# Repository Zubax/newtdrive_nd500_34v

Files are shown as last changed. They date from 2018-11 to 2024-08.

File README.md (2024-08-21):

# NewtDrive ND500-34V / Zubax Sadulli

Sadulli is an open-hardware reference design of a 500 W integrated propeller drive based on the
[Mitochondrik LV](http://zubax.com/mitochondrik-lv) motor control chip.
It includes a motor and its control electronics in a single compact unit.

The main design goal is to create a compact yet sophisticated motor controller that can be integrated with relatively
small BLDC and PMSM motors (about 40-45 mm in diameter) in a single unit.
Being equipped with a standard mounting hole pattern,
Sadulli can be used as a drop-in replacement for regular standalone motors in various UAV applications.

## Specifications

- Operating voltage range: 4-8S Li-ion LiCoO<sub>2</sub>, 11-34 V
- Maximum continuous power 500 W
- Maximum continuous phase current amplitude 40 A
- [Cyphal](https://telega.zubax.com/)/CAN (formerly UAVCAN) interface compatible with the DS-015 drone standard
- Solderless integration

Sadulli consists of two main parts: a COTS motor and the ESC.
This repository contains the ESC hardware source files only.
There are two design variants of the Sadulli drive.
All of them share the same ESC design.

Variant  | Motor                 | Propeller diameter [inch] | Propeller pitch [inch] | Mass [g]
-------- | --------------------- | ------------------------- | ---------------------- | --------
Alakdan  | Scorpion MII-4010     | 17                        | 6.2                    | 193
Nudo     | N/A                   | N/A                       | N/A                    | 62

Alakdan | Nudo
--|--
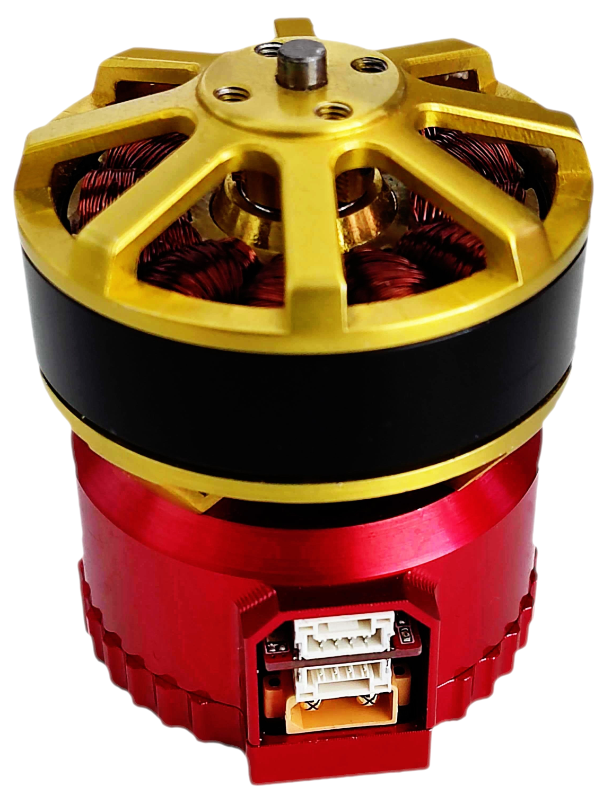
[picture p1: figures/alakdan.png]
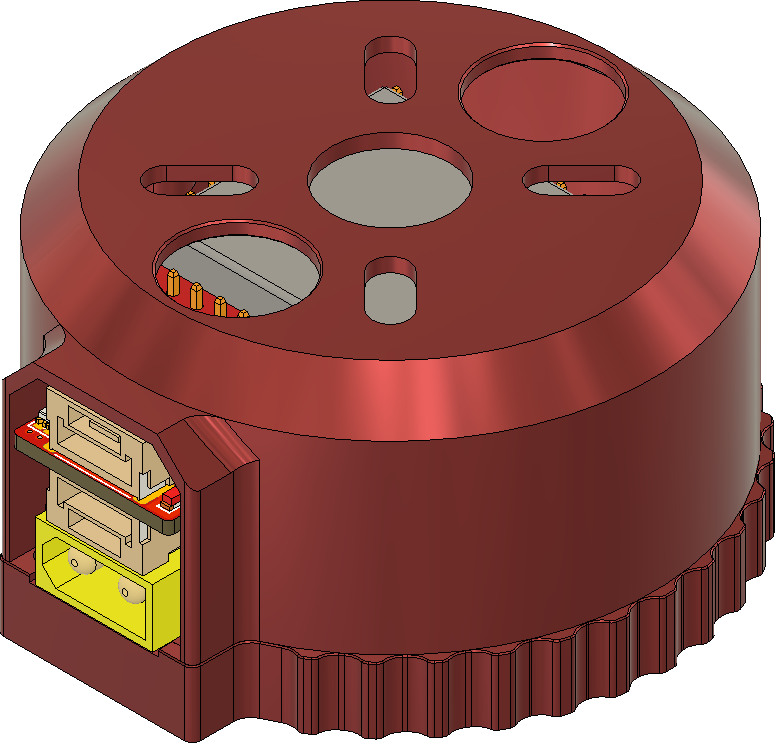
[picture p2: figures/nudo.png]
 | 

Sadulli is equipped with a single non-redundant Cyphal/CAN interface.
The input power is supplied through a standard XT30 male connector.
The device can deliver 5V to the Cyphal/CAN power delivery network if the respective configuration option is enabled.

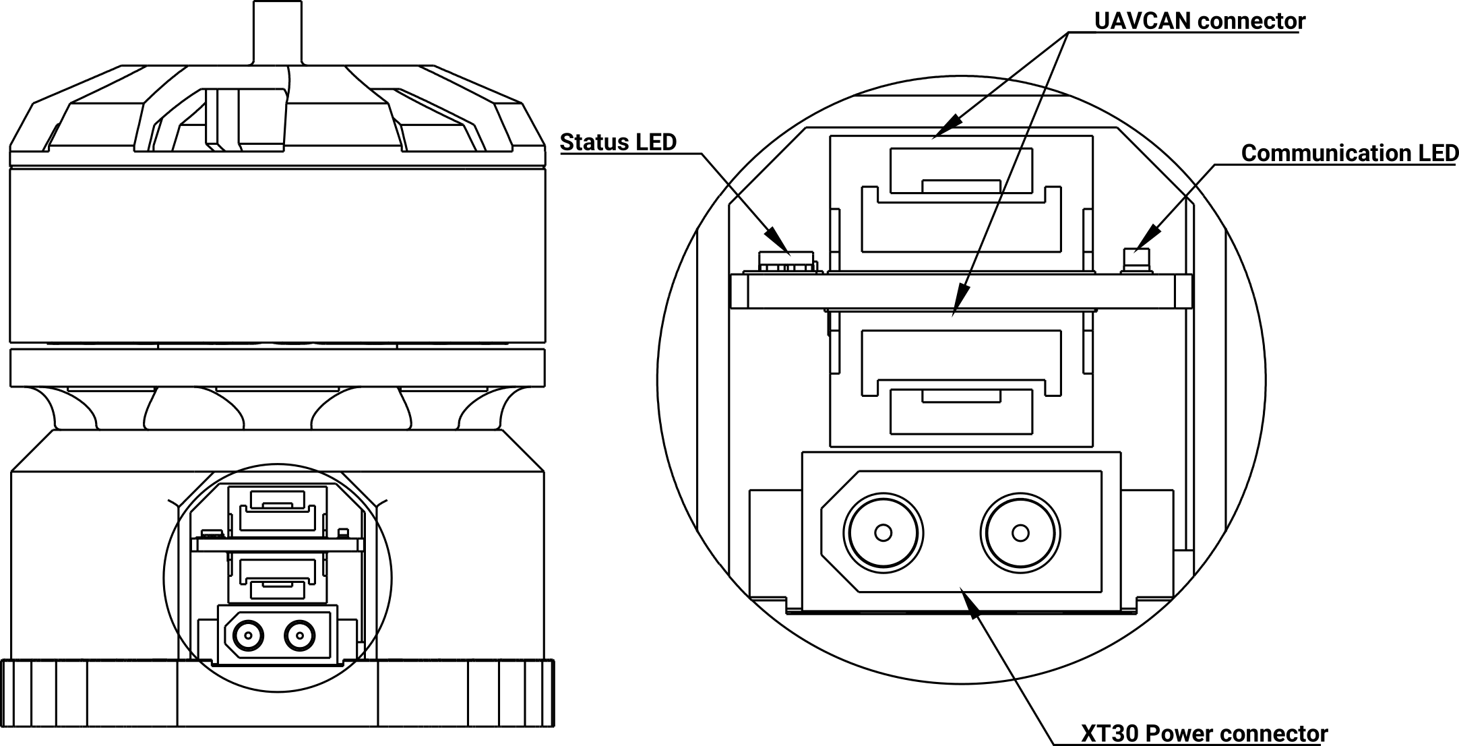
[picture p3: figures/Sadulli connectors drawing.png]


Under the hood, Sadulli is a construction of three PCBs (excluding the Mitochondrik).

<p align="center">
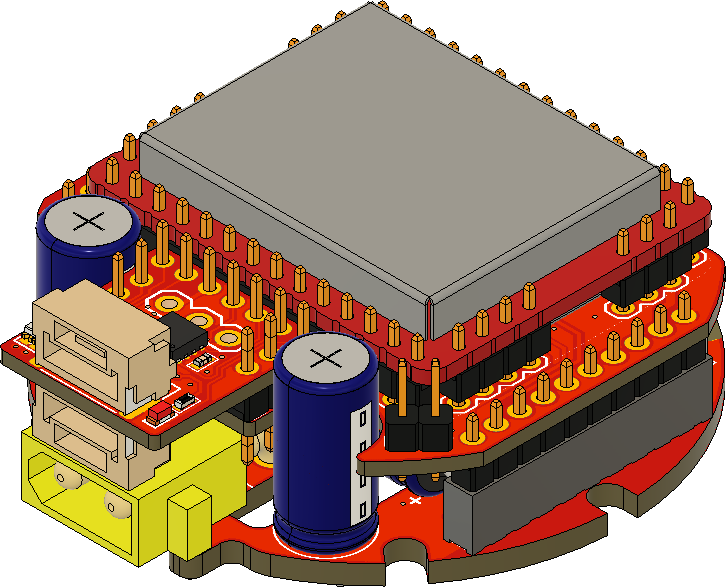
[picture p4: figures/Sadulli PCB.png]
Sadulli PCB

</p>

The main PCB that determines most of Sadulli's properties is the power stage PCB.
The power stage is composed of three [BUK9K6R2-40E](https://www.digikey.com/products/en?keywords=1727-7274-1-ND)
MOSFET arrays.

Parameter                                               | Value
------------------------------------------------------- | -------------------
Drain to Source Voltage (V<sub>ds</sub>)                | 40 V
Current - Continuous Drain (I<sub>d</sub>) @ 25°C       | 40 A
R<sub>ds on</sub> (Max) @ I<sub>d</sub>, V<sub>gs</sub> | 6 mOhm @ 25 A, 10 V
Gate Charge (Q<sub>g</sub>) (Max) @ V<sub>gs</sub>      | 35.4 nC @ 10 V

The resistance of the phase current shunts is 3 mOhm.

The bulk capacitor bank is formed with 6
[68µF aluminum electrolytic capacitors](https://www.digikey.com/product-detail/en/w-rth-elektronik/860020673014/732-8860-3-ND/5727097).

### Telega configuration

The Mitochondrik LV module installed in Sadulli needs to be configured such that it is aware of the parameters of the power stage
(and the motor).
To achieve this, upload the following configuration:

```yaml
# Refer to the Mitochondrik-LV datasheet for the explanation of how the parameter values have been found.
vsi.bridge_resistance:    [0.003, 0.006, 0.003, 0.006, 0.003, 0.003]                            # [ohm]
vsi.phase_current_gain:   [33.333333333333, 33.333333333333, 8.333333333333, 8.333333333333]    # [ampere/volt]
vsi.phase_current_stderr: [0.2, 0.2, 0.1, 0.1]                                                  # [ampere]
vsi.thermistor_v2k:       [223.15, 100.0, 0.0]                                                  # for MCP9700

motor.current_ctl_bwr:  0.04
motor.current_max:      38.0
motor.mechanical_ratio: 7                   # The motor has 14 poles.
motor.inductance_dq:    [29.0e-6, 29.0e-6]
motor.resistance:       0.0508
motor.flux_linkage:     0.002115
motor.current_ramp:     5000.0
motor.voltage_ramp:     20.0
# The thermistor coefficients are valid for:
# R_pull = 1.2 kohms; R_io = 0; V_pull = 3.3 V
# Thermistor models: KTY81/120, KTY81/110, KTY81/121, KTY81/122, KTY81/150, 102PS1J, 102PS1G.
motor.thermistor_v2k: [151.24172662, 36.46076996, 40.65372514]

aux.pull: +1                    # Pull up the thermistor input.

sys.debug: false                # Turn off the in-circuit debug interfaces to enhance EMI immunity.
sys.golden: sys. vsi. motor. aux.pull # Retain these parameter groups across a factory reset.
```

Refer to the Telega Reference Manual for details.

## Release notes

### Sadulli v1.5 (May 2023)

* Added Alakdan variant using Scorpion MII-4010 motor.
* Removed Grosso and Piccino variants using SunnySky motors.
* Updated assembly guide.
* Increased the hardware over-current protection limit (R1 on the connectors PCB increased to 27k).
* Added thermistor alternatives:

Original  | Alternatives
--------- | -----------------
KTY81/120 | KTY81/110, KTY81/121, KTY81/122, KTY81/150, 102PS1J, 102PS1G

### Sadulli v1.0 (January 2021)

First stable release. There have been no substantial changes compared to the pre-production revision.

## License

This project is licensed under the terms of [CC-BY 4.0](https://creativecommons.org/licenses/by/4.0/).

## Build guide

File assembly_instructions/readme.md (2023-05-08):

# Zubax Sadulli V1.5 manufacturing instructions

Prior to starting the assembly make sure that all the items from the list below are present.

Item                          | Amount| Part number                                                            | Description
------------------------------|-------|------------------------------------------------------------------------|-------------------------------------------------------
Motor                         | 1     | Scorpion MII-4010                                                      | BLDC motor for Alakdan.
Housing top                   | 1     |                                                                        | Milled from aluminum.
Housing bottom                | 1     |                                                                        | Milled from aluminum.
Housing screw                 | 4     | DIN 965 20 mm / M2.5x16                                                | Fastening both parts of the housing together.
Motor screw                   | 4     | DIN 7984 4 mm / M3x4                                                   | Fastening the motor to the top part of the housing.
Thermal pad                   | Dia 42 mm | Arctic Cooling ACTPD00018A, ACTPD00005A, or ACTPD00002A            | Sinks the heat to the bottom part of the housing.
Connectors PCB                | 1     |                                                                        |
Logic PCB                     | 1     |                                                                        |
Power stage PCB               | 1     |                                                                        |
Thermistor                    | 1     | NXP KTY81/120, NXP KTY81/110, NXP KTY81/121, NXP KTY81/122, NXP KTY81/150, Littelfuse 102PS1J, or Littelfuse 102PS1G | PTC thermistor with pre-soldered extension wires.

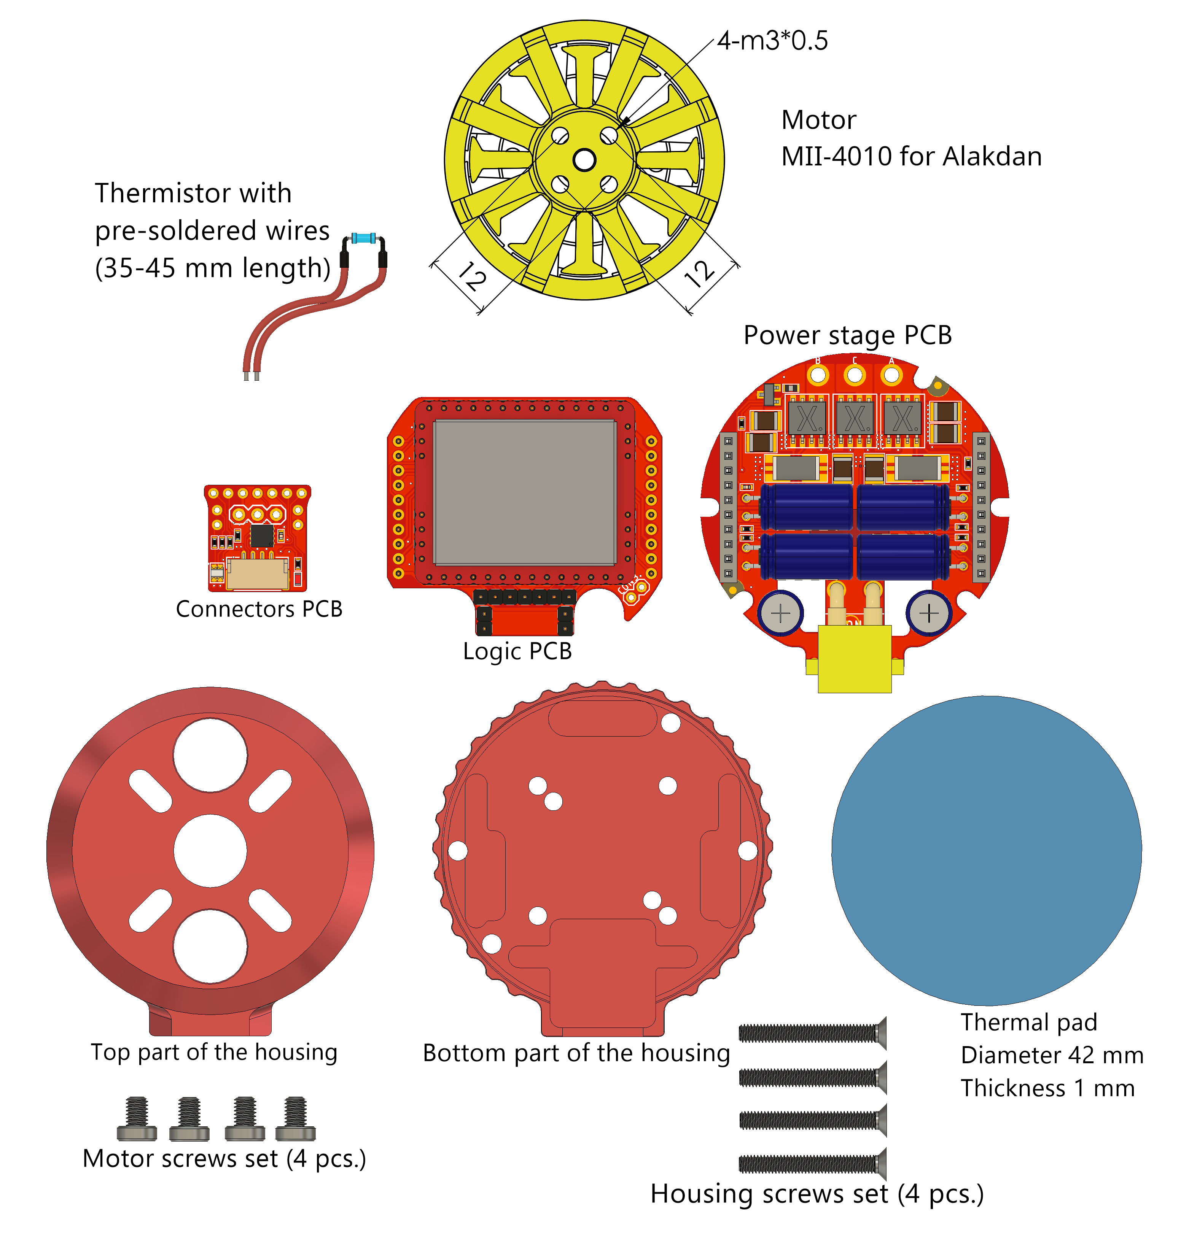
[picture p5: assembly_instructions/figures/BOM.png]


### Assembly Instructions

The whole assembly process may be divided in several sequential steps:

1. Connector and Power stage PCB SMD assembly.

2. Logic PCB assembly. This is manual operation that needs to be precise. 
    * 2 mm male pin headers need to be placed in a repeatable way on the PCB as this may affect assemblability of the device. 
Solder the shorter side to the board ensuring that the headers are straight and at a right andle to the PCB. 
To simplify the process, solder 1 pin first then adjust the angle before soldering the rest. 
    * Attach Mitochondrik LV to the Logic PCB via 2 mm pin headers.
    * Attach Connector PCB to Logic PCB via 2 mm pin headers.
    * Attach the Power stage PCB to Logic PCB via 2 mm pin headers.
    * Refer to the images below for the proper placement.

<p align="center">
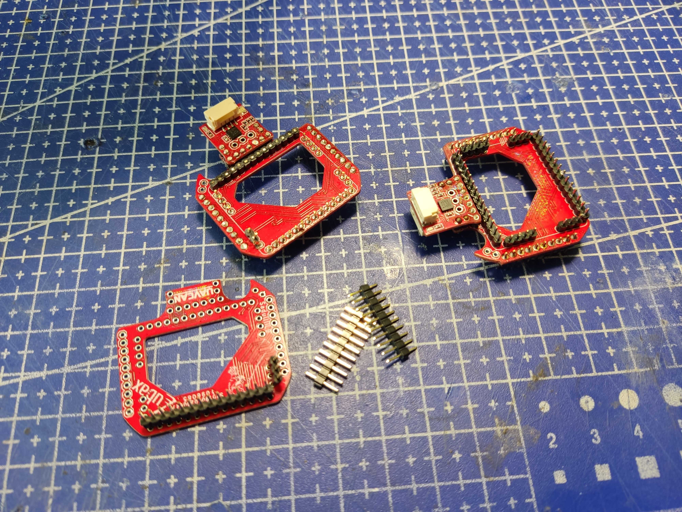
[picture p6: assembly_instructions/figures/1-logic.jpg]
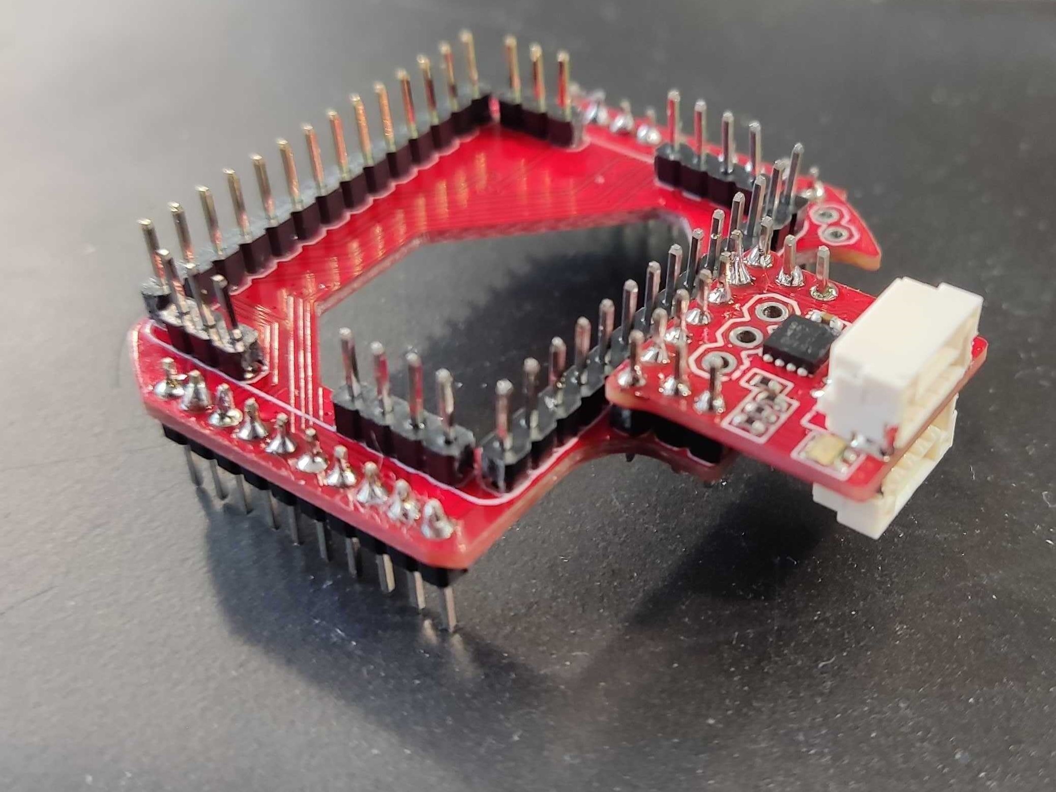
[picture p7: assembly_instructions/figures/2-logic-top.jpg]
<br>
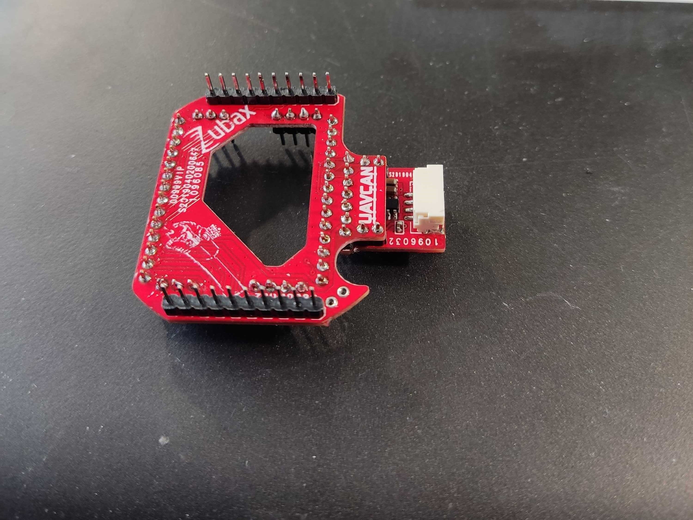
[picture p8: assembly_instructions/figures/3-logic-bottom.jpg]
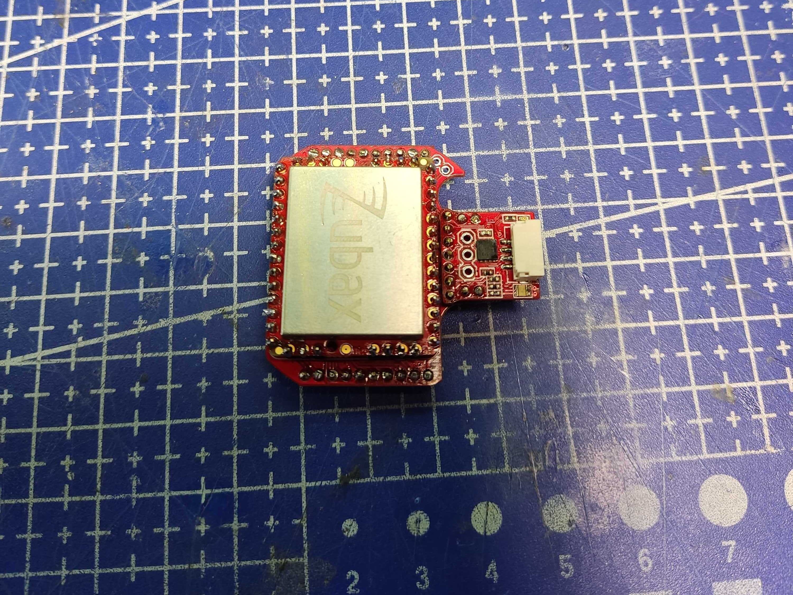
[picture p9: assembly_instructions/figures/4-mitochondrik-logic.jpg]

</p>

3. Motor modification. 
    * Remove the motor retainer ring.
    * The phase wires should be rerouted straight down.

<p align="center">
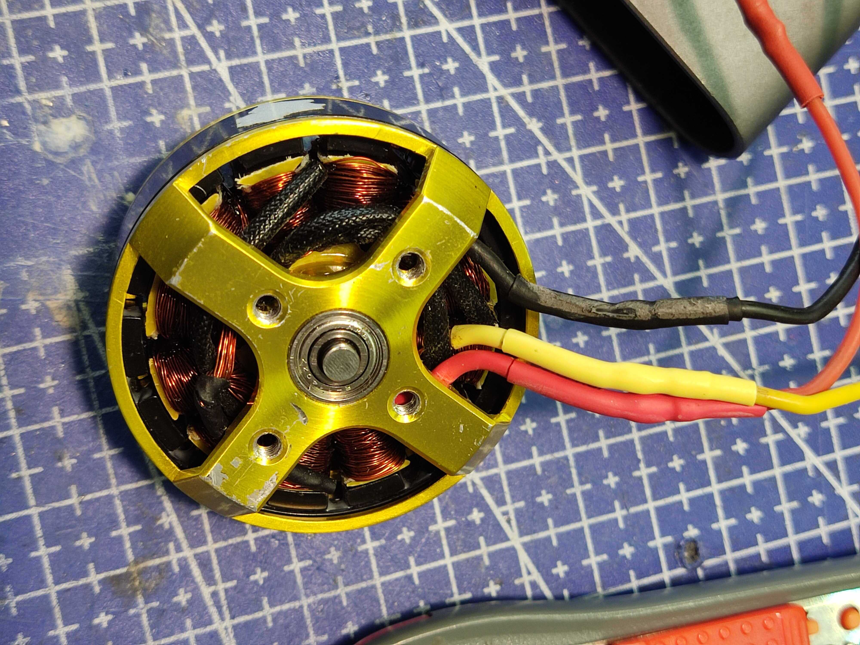
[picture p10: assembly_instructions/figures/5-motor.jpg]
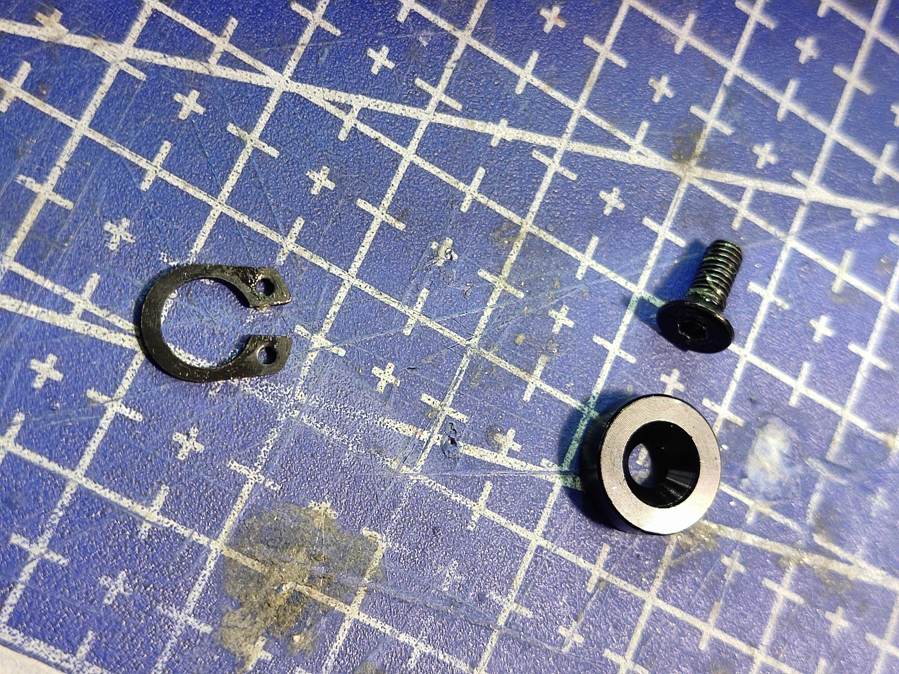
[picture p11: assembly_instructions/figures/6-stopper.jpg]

</p>

4. Thermistor preparation. See photos below for reference.
    * Mix both parts of the epoxy resin in a plastic container using a wooden or plastic mixing tool.
    * Dip the thermistor into the mixture. Only a small amount of glue is needed.
    * The thermistor should be glued directly to the motor windings with epoxy resin
(care must be taken to avoid ingress of epoxy into the motor bearing). Wipe excess with tissue.
    * It can also be placed in between 2 coils, directly on top of a coil, 
or if the coils are flat - glue the side of the thermistor with the flat silver plate.
    * It may be necessary to add more resin to both sides of the thermistor. 
Use a cotton bud to apply more glue carefully.
    * Wait for the epoxy resin to solidify - around 5 minutes.
    * Trim the leads of the thermistor to 2-3 mm.
    * Get 2 pieces of thin wires (0.3-0.6 mm dia). The wires' length should be ~35-45 mm. Remove a portion of the outer casing.
    * Add solder to the ends of the wires (3-5 mm). Add solder to the thermistor leads. 
    * Solder the wire to the lead side-by-side to ensure sufficient contact between the two.
    * Get 2 pieces of the smallest heat shrink tube. Cut to 2-3 mm in length. Cover the connection point and apply heat with a heat gun.

<p align="center">
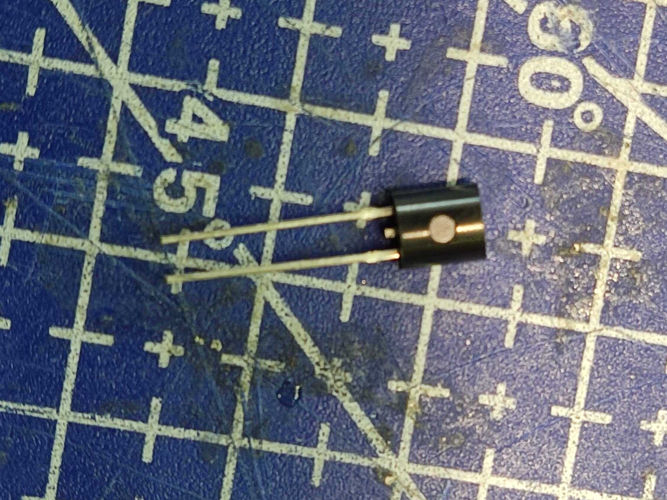
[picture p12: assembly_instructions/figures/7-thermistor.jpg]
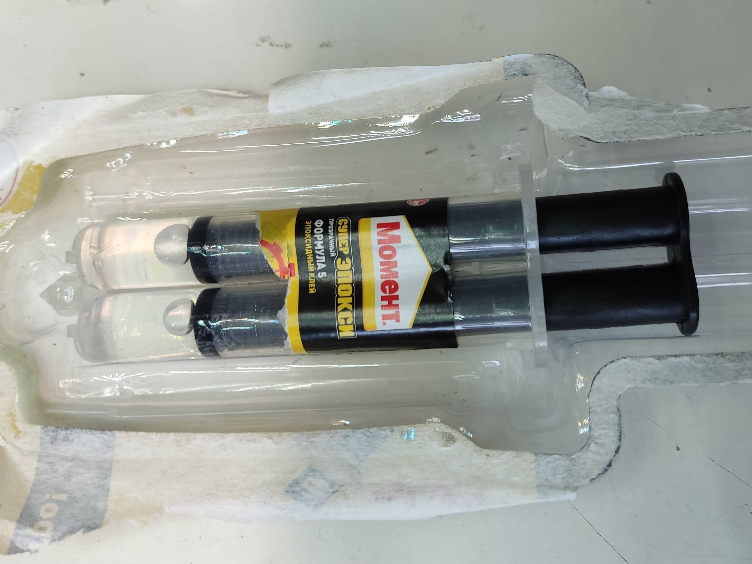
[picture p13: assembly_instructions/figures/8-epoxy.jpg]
<br>
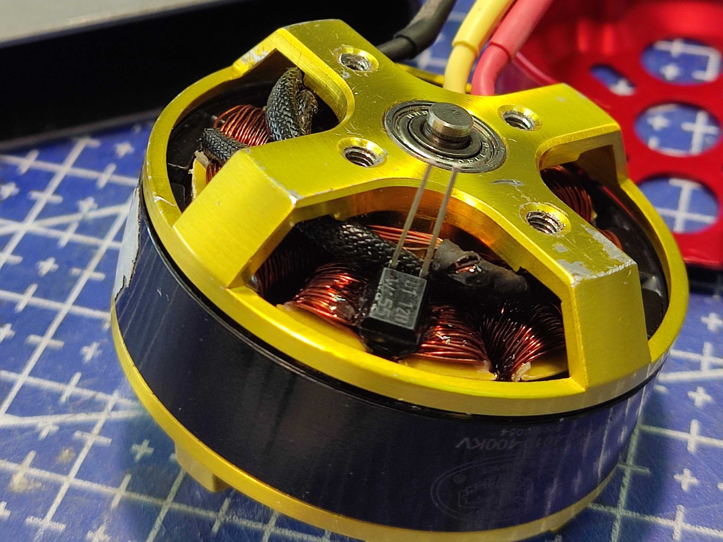
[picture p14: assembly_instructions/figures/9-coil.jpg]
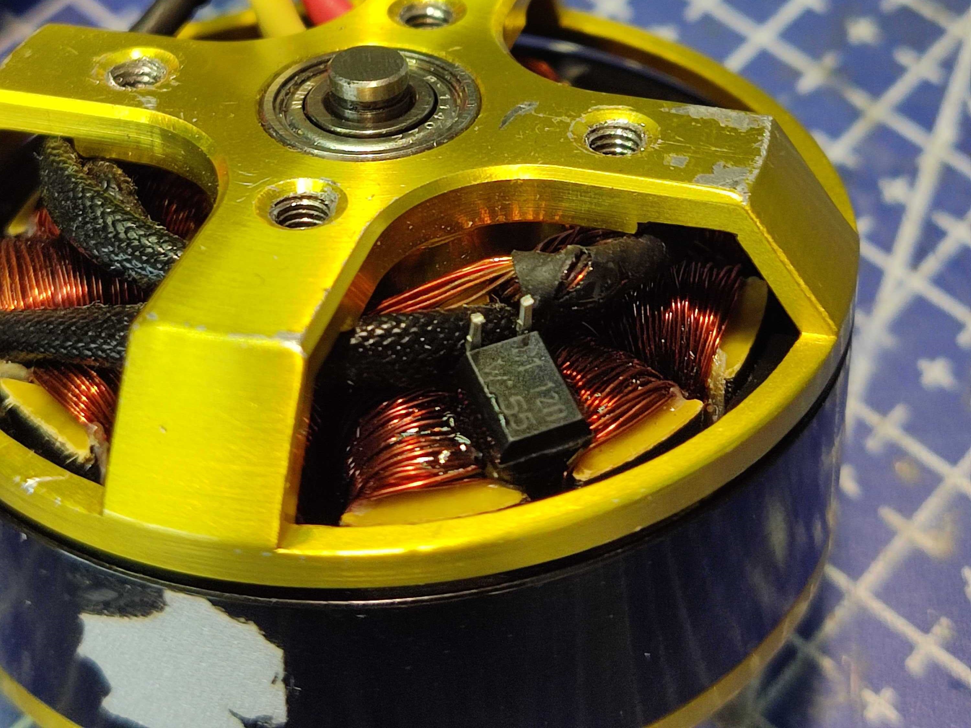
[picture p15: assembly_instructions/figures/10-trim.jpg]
<br>
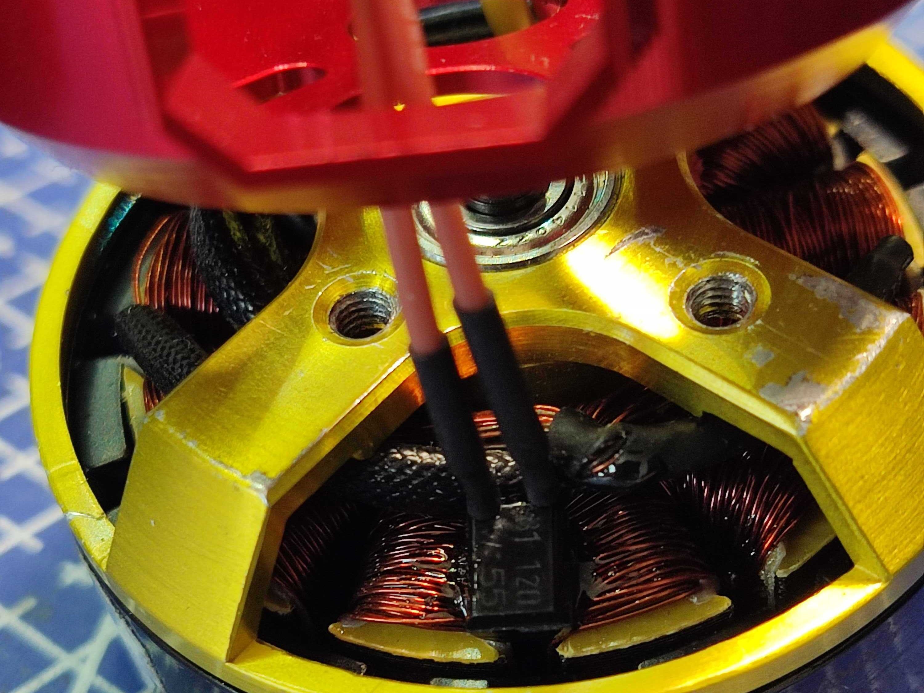
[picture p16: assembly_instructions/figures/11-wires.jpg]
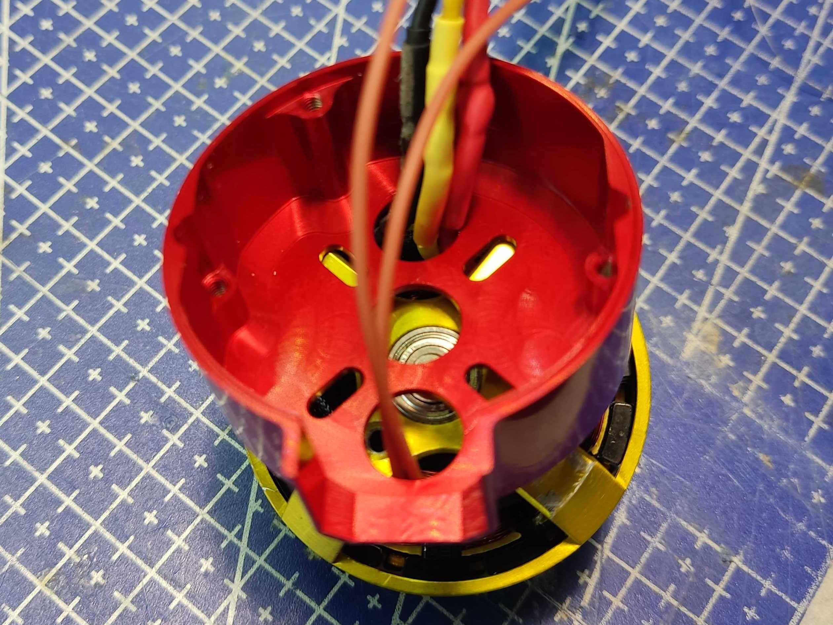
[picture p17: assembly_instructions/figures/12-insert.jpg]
<br>
</p>

5. Housing Attachment. See photos for reference.
    * Insert the motor phase wires and the thermistor wires through the housing holes. Ensure proper placement.
    * Get 4 pieces of DIN 7984 4 mm (motor screws). Attach the motor to the top housing. Use threadlock glue.
Ensure that the screws don't touch the coils and that no moving part of the motor is touching the enclosure.
    * Trim the motor phase wires to ~30-35 mm (measuring from the bottom of the motor).
    * Remove the insulation. Twist the wires. Add solder to the ends of each wire (3-5 mm).
    * Place the assembly on a vise to secure it. Use rubber protection pads so that the motor isn't scratched.
    * Solder the phase wires to 3 pads on the PCB.
    * **The phase wires shall be soldered such that a positive setpoint drives the motor clockwise (viewed from the top).**
If the observed direction is different, any two phase wires of the three are to be swapped.
    * Trim the thermistor wires and solder to 2 pads on the PCB. See photo for correct placement.
    * Add thermal pad to the inside of the bottom housing. 
    * The thermal pad has the shape of a circle with a diameter of 40-42 mm, 1 mm thickness.
    * Attach bottom housing to the top housing using 4 housing screws (DIN 965 20 mm / M2.5x16)

<p align="center">
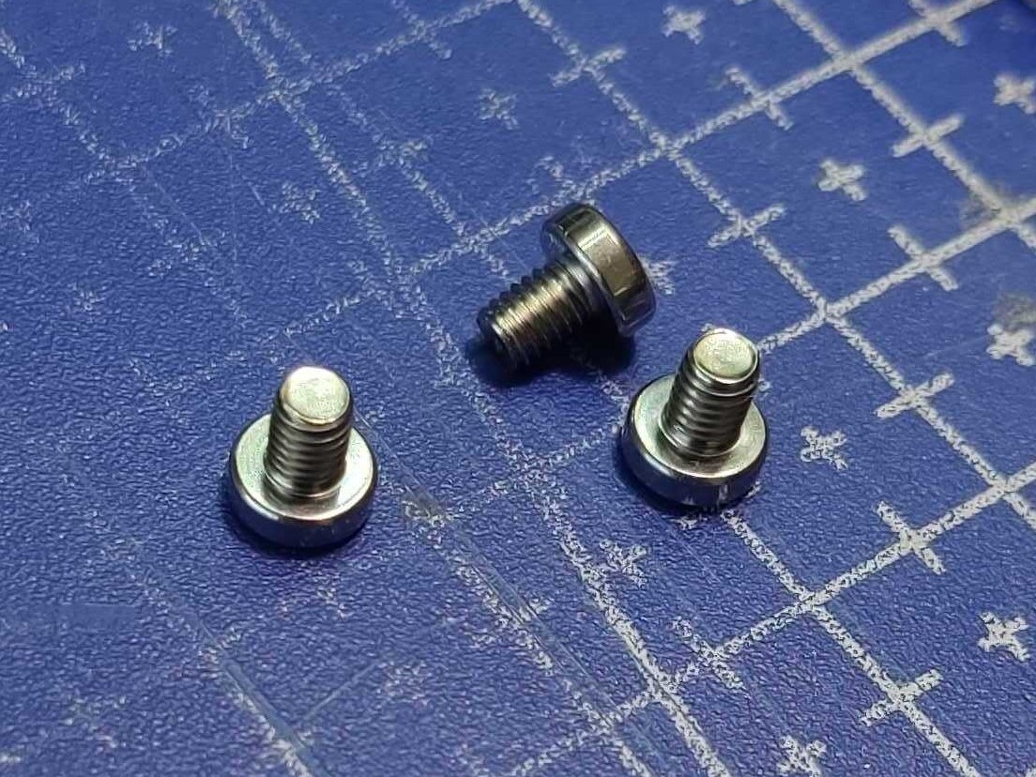
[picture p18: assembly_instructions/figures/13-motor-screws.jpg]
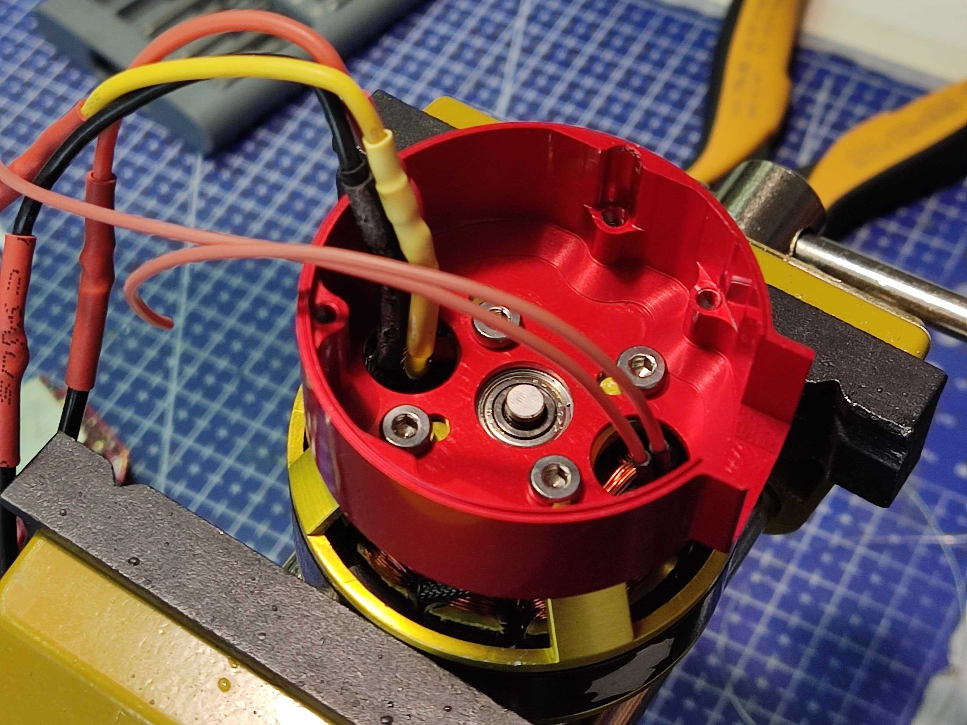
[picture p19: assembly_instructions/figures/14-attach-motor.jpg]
<br>
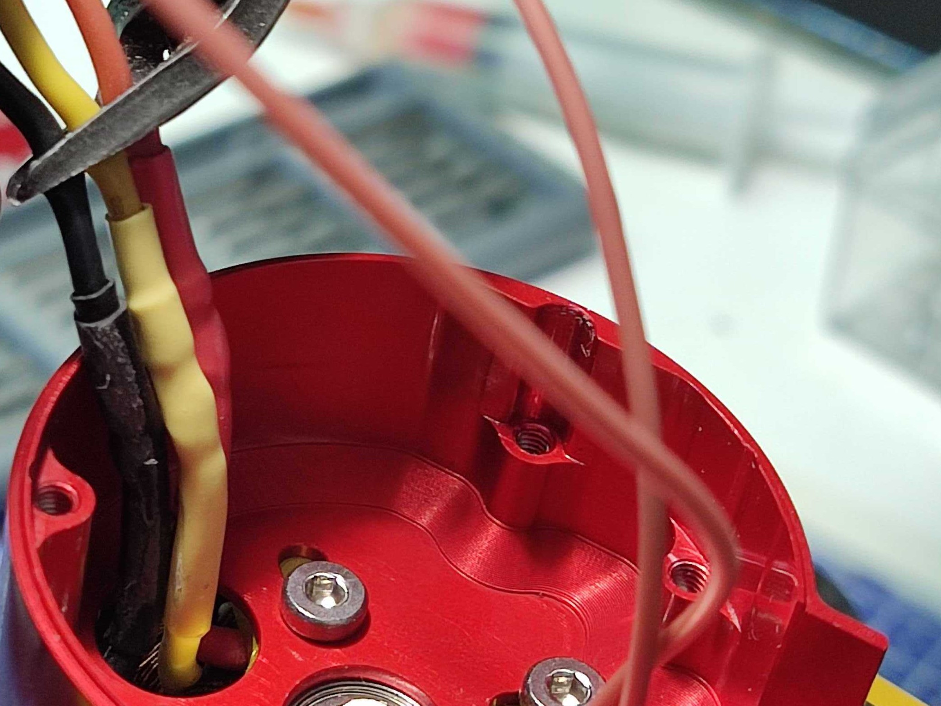
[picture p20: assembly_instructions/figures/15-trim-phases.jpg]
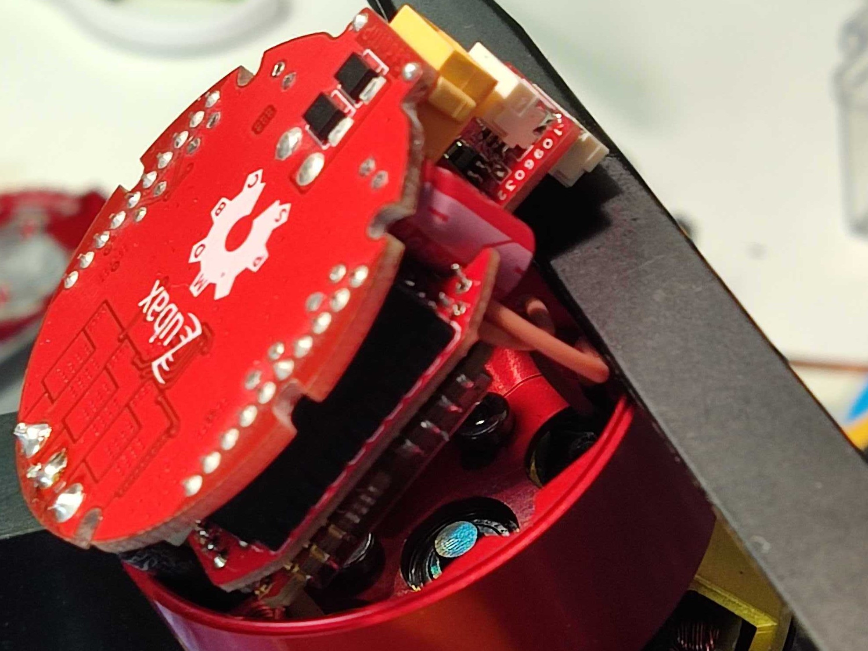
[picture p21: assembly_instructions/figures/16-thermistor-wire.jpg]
<br>
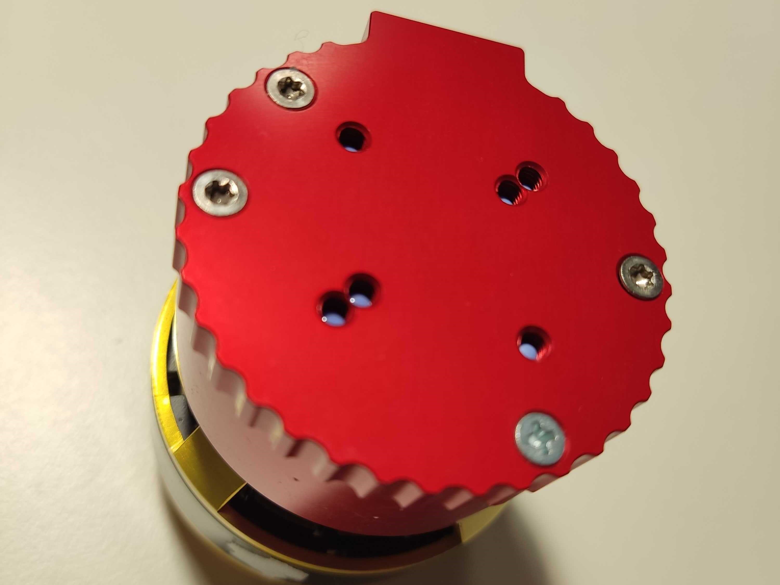
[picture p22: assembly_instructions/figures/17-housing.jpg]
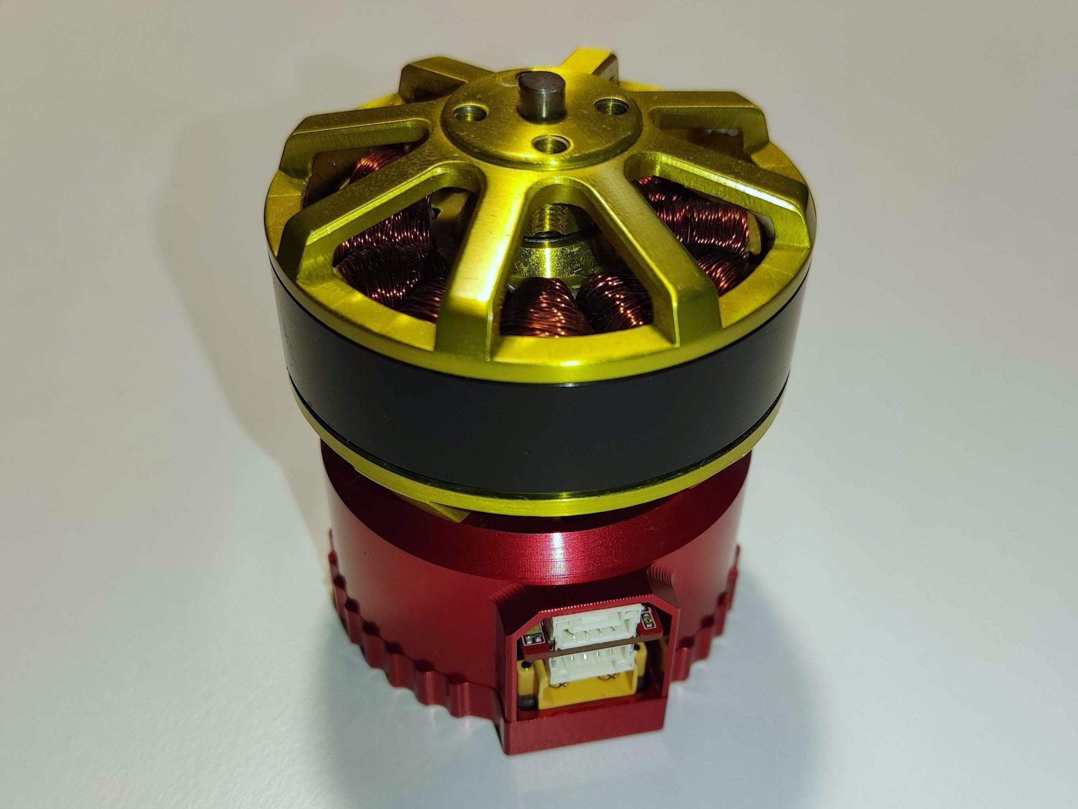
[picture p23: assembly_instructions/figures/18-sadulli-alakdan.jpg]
<br>
</p>

6. Test using DrWatson (internal).
    * **If the motor spins counterclockwise (viewed from the top) during the DrWatson test, remove the bottom housing and swap any two phase wires.**

For the detailed assembly process of Sadulli v1.0 (Grosso/Piccino) please check the video: https://youtu.be/bqTBei1wUUw

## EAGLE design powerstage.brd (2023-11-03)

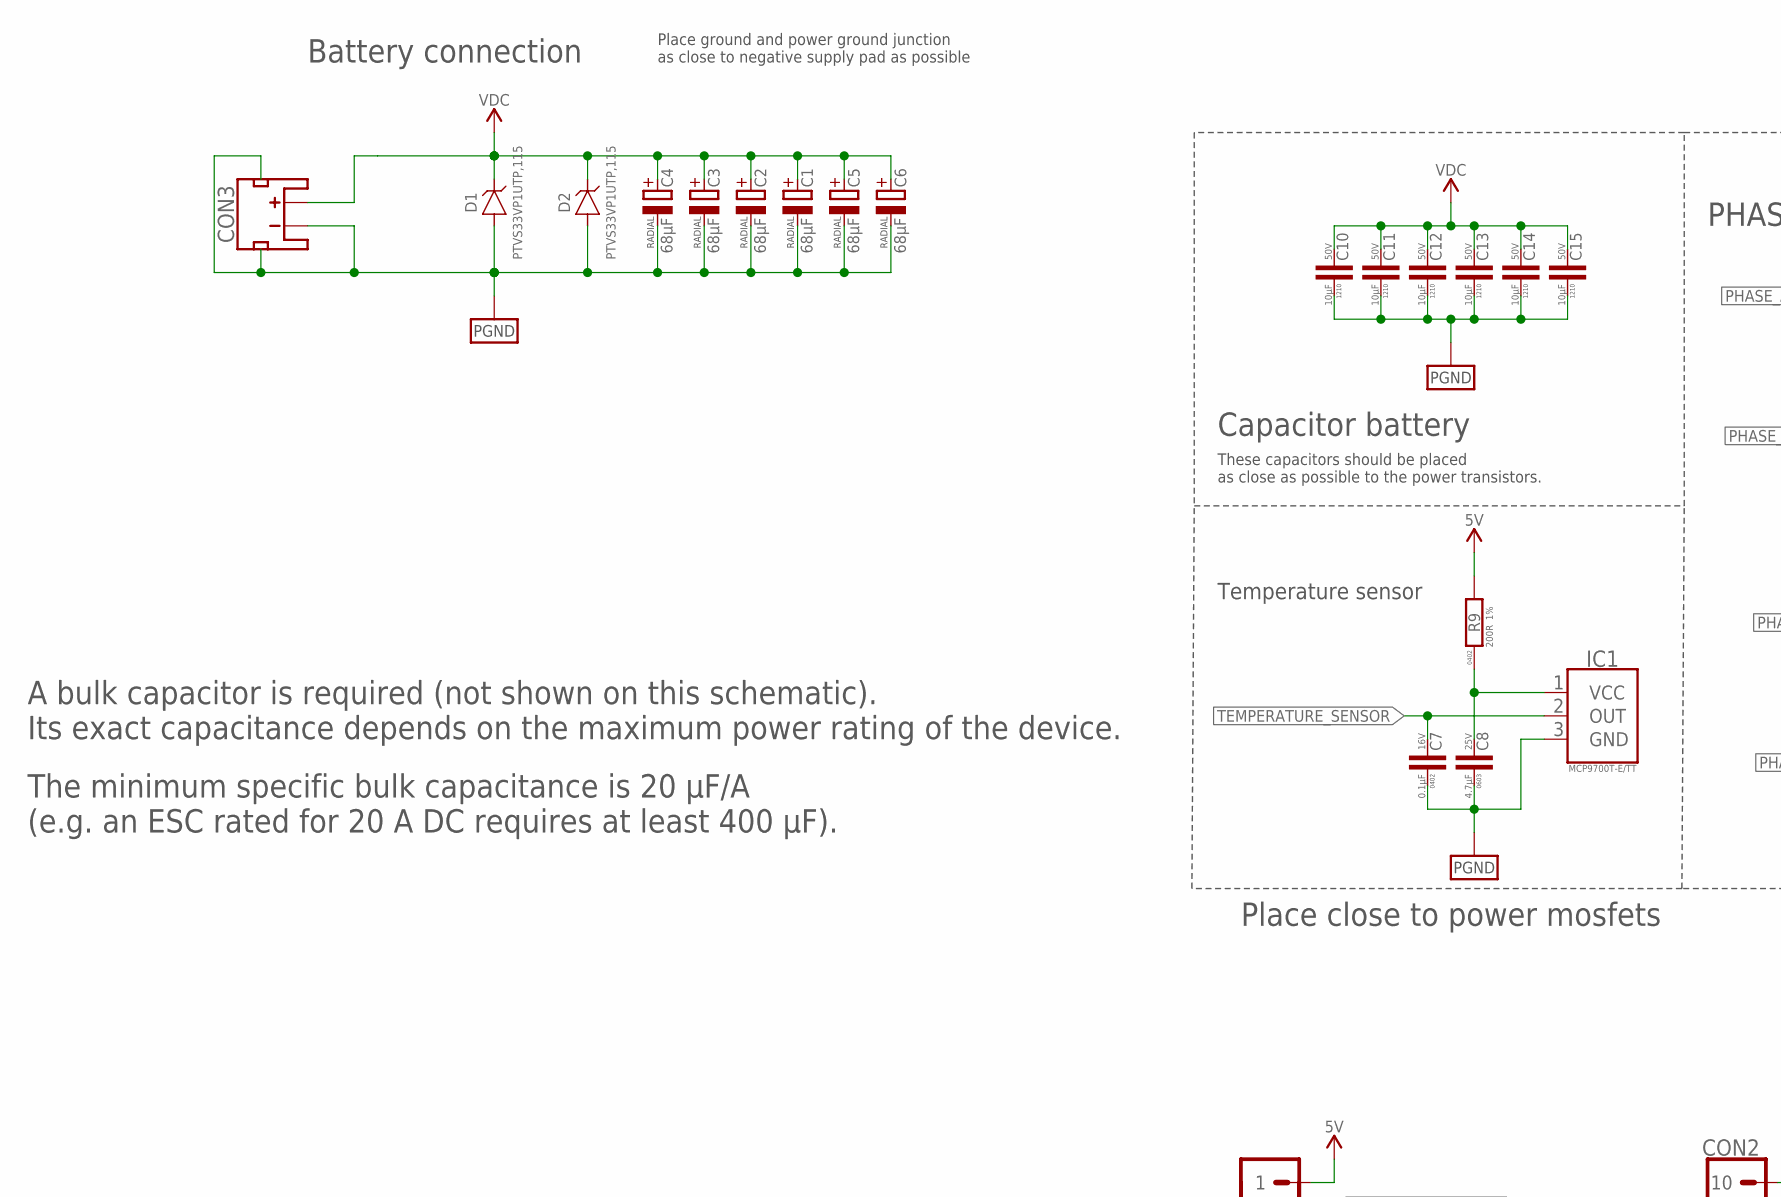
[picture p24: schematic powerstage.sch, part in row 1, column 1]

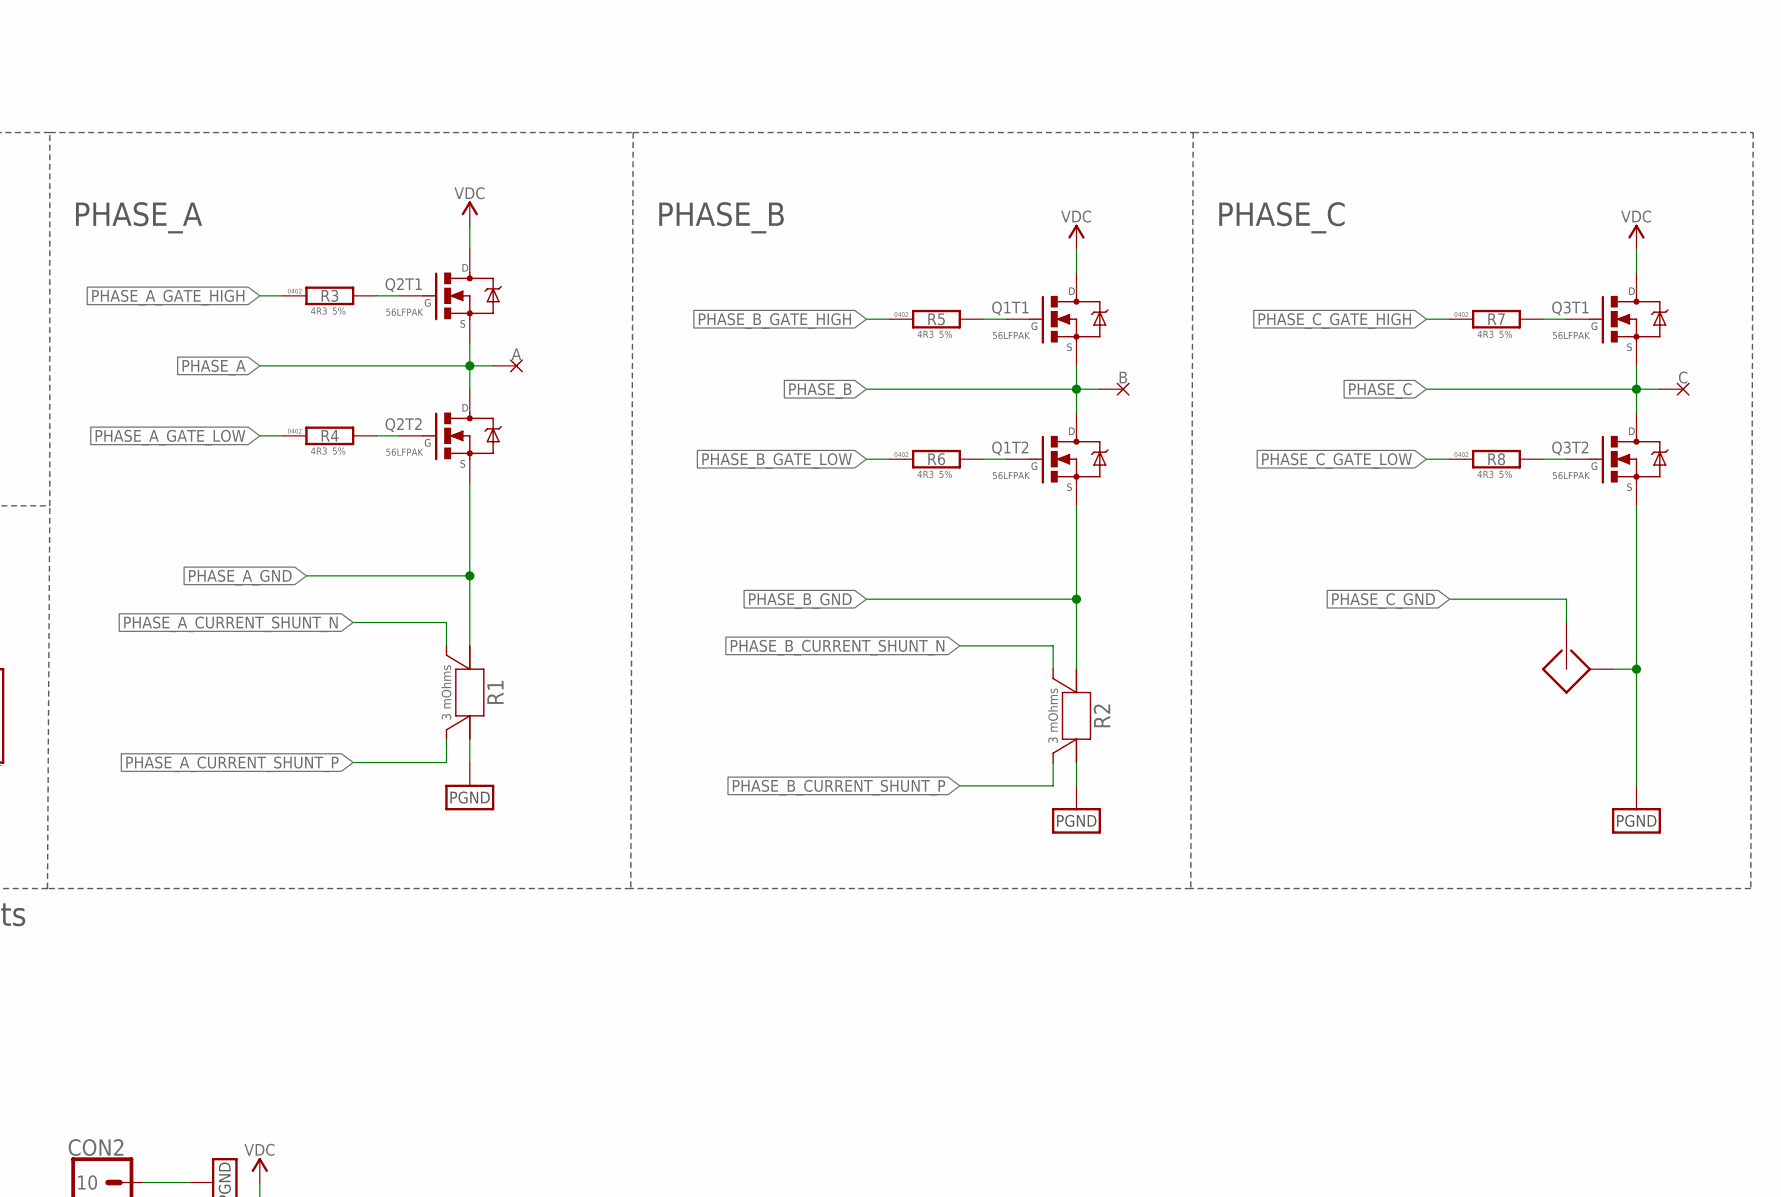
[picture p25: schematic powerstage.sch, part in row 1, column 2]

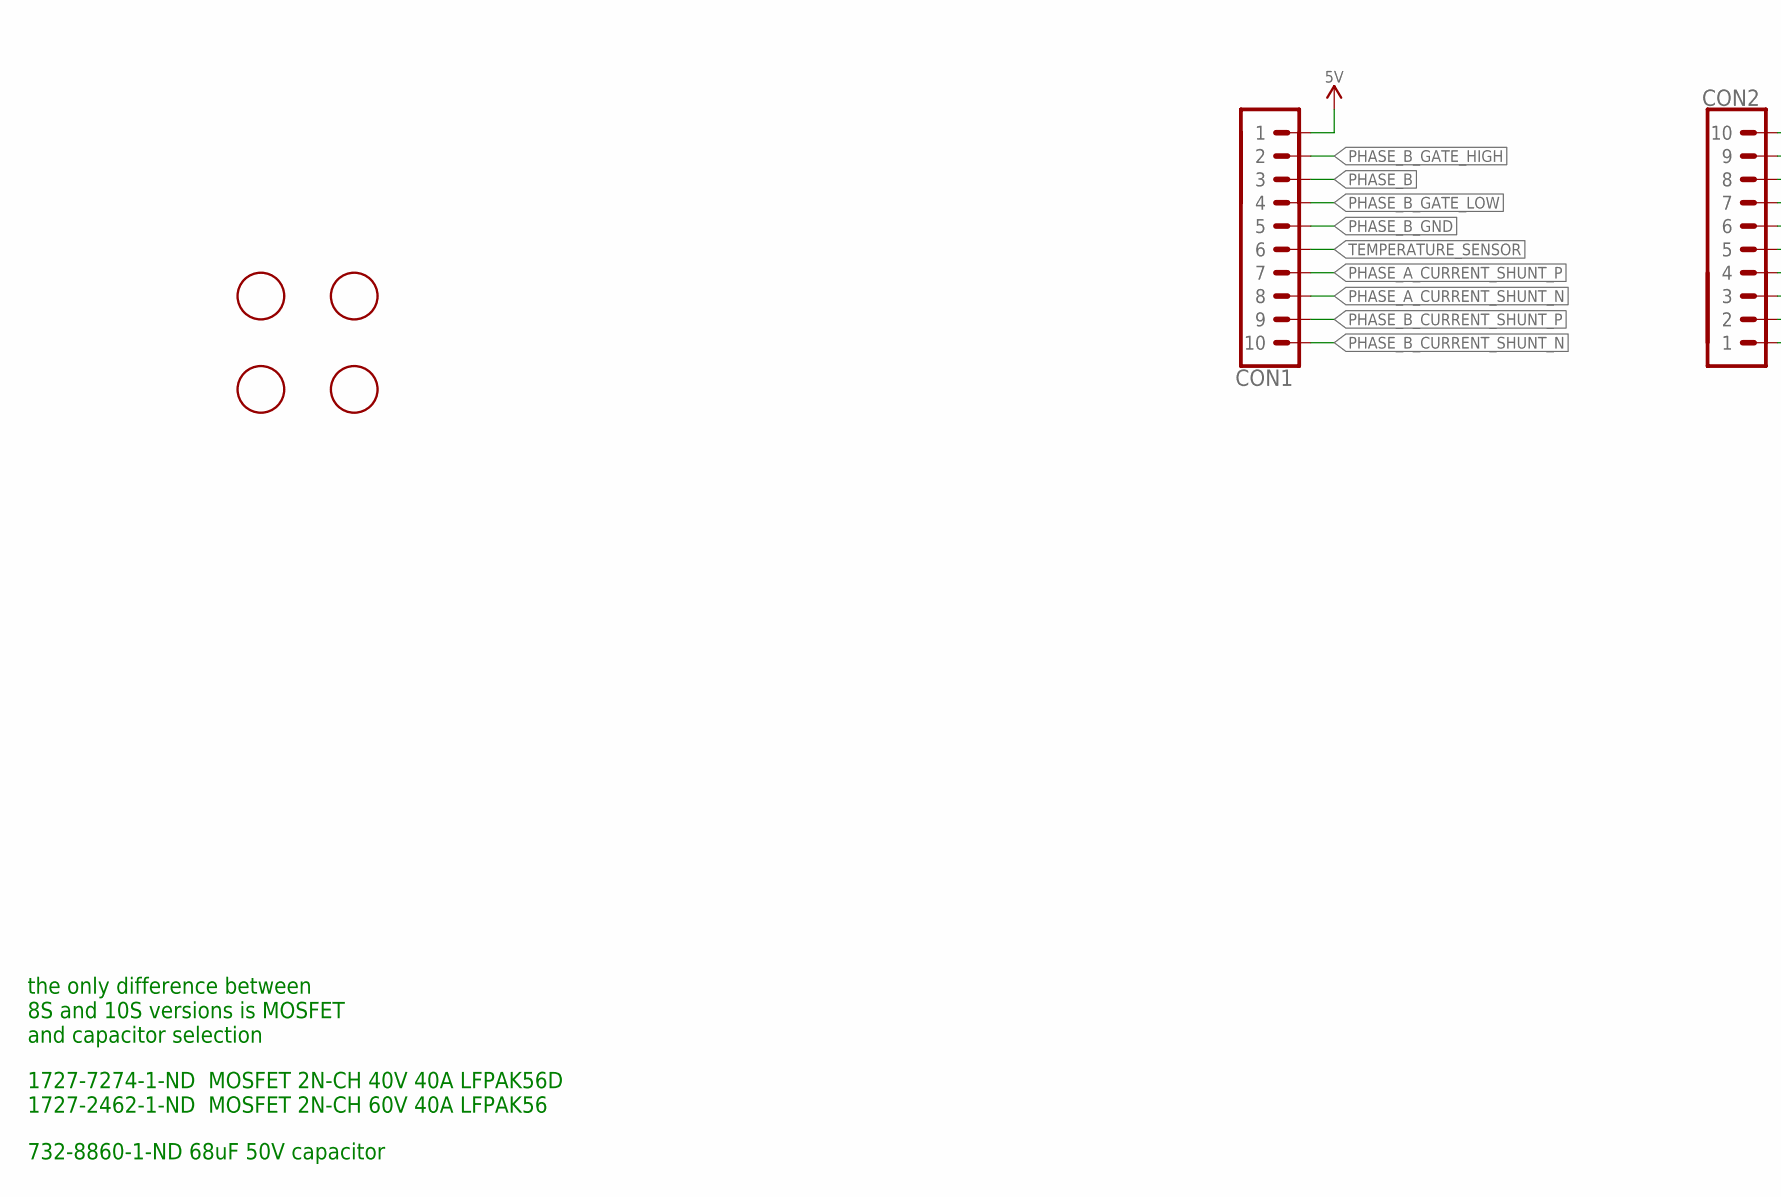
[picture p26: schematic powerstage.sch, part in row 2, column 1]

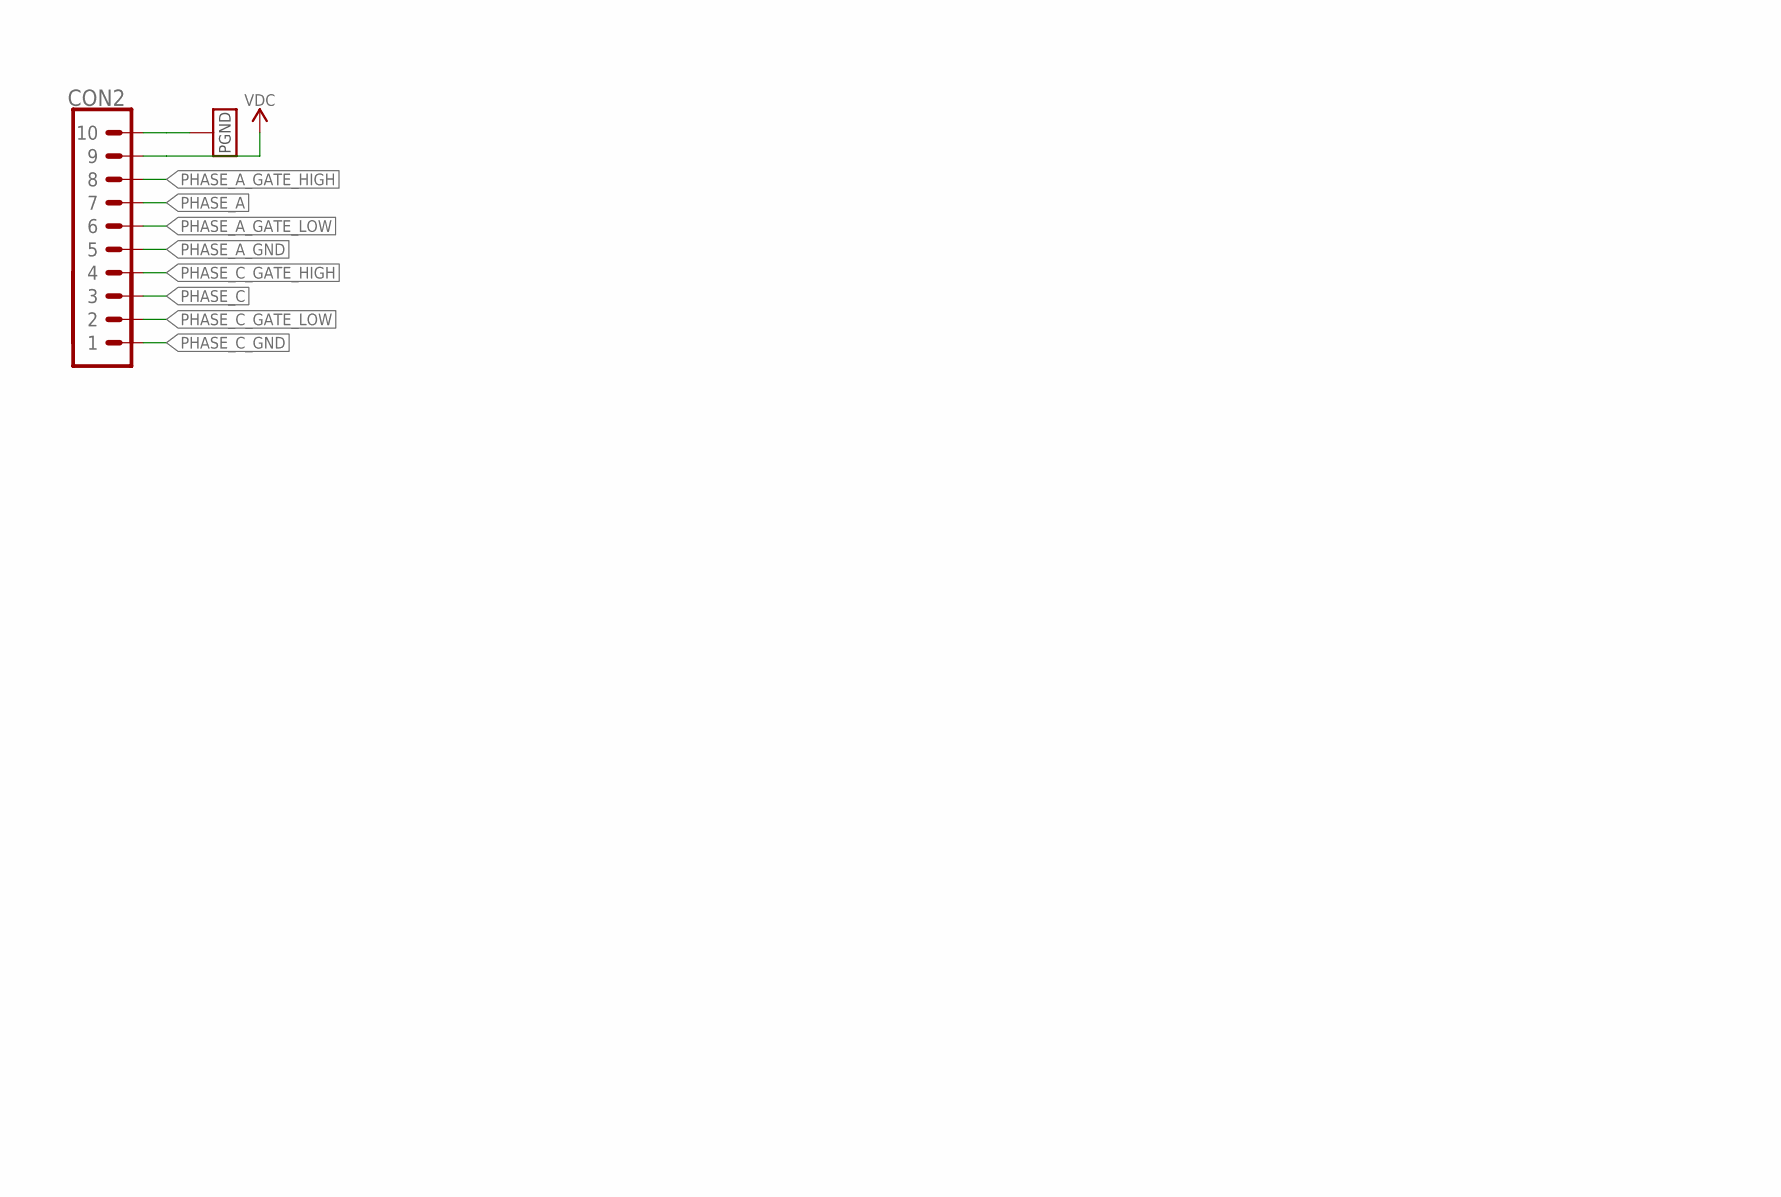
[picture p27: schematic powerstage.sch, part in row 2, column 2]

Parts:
A: PAD-HOLE_2; HOLE_2
B: PAD-HOLE_2; HOLE_2
C: PAD-HOLE_2; HOLE_2
C1, C2, C3, C4: 68µF; RADIAL_6.3X12.5-RA
C5, C6: 68µF; RADIAL_6.3X12.5; DIGIKEY# 732-8860-1-ND
C7: 0.1µF; C0402
C8: 4.7µF; C0603
C10, C11, C12, C13, C14, C15: 10µF; C1210
CON1, CON2: PINHEAD_1X10-2-FEMALE; 1X10-PTH_2-FEMALE
CON3: BATTERY_CON-2P-XT30-RA; XT30-RA
D1, D2: PTVS33VP1UTP,115-36V-SOD128; SOD128
IC1: MCP9700; SOT23B-3
Q1, Q2, Q3: BUK9K6R2-40E,115; SOT-1205
R1, R2: 3 mOhms; R2512-KELVIN
R3, R4, R5, R6, R7, R8: 4R3; R0402
R9: 200R; R0402
S1: SENSE; SENSE-0.6
U$8, U$9, U$10, U$12: FIDUCIALMOUNT; FIDUCIA-MOUNT

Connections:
unnamed: Q2.2 (G), R3.2
unnamed: Q2.4 (G), R4.2
unnamed: Q1.2 (G), R5.2
unnamed: Q1.4 (G), R6.2
unnamed: C8.P$2 (2), IC1.1 (VCC), R9.1
unnamed: Q3.2 (G), R7.2
unnamed: Q3.4 (G), R8.2
PGND: C1.-, C2.-, C3.-, C4.-, C5.-, C6.-, C7.1, C8.P$1 (1), C10.1, C11.1, C12.1, C13.1, C14.1, C15.1, CON2.10, CON3.-, CON3.P$3 (PAD1), CON3.P$4 (PAD2), D1.A, D2.A, IC1.3 (GND), Q3.3 (S), R1.2, R1.22 (2), R2.2, R2.22 (2), S1.SHELL (SHELLL)
PHASE_A: A.P$1, CON2.7, Q2.1 (S), Q2.5 (D), Q2.6 (D), Q2.EP-5-6 (D)
PHASE_A_CURRENT_SHUNT_N: CON1.8, R1.S1
PHASE_A_CURRENT_SHUNT_P: CON1.7, R1.S2
PHASE_A_GATE_HIGH: CON2.8, R3.1
PHASE_A_GATE_LOW: CON2.6, R4.1
PHASE_A_GND: CON2.5, Q2.3 (S), R1.1, R1.11 (1)
PHASE_B: B.P$1, CON1.3, Q1.1 (S), Q1.5 (D), Q1.6 (D), Q1.EP-5-6 (D)
PHASE_B_CURRENT_SHUNT_N: CON1.10, R2.S1
PHASE_B_CURRENT_SHUNT_P: CON1.9, R2.S2
PHASE_B_GATE_HIGH: CON1.2, R5.1
PHASE_B_GATE_LOW: CON1.4, R6.1
PHASE_B_GND: CON1.5, Q1.3 (S), R2.1, R2.11 (1)
PHASE_C: C.P$1, CON2.3, Q3.1 (S), Q3.5 (D), Q3.6 (D), Q3.EP-5-6 (D)
PHASE_C_GATE_HIGH: CON2.4, R7.1
PHASE_C_GATE_LOW: CON2.2, R8.1
PHASE_C_GND: CON2.1, S1.IN
TEMPERATURE_SENSOR: C7.2, CON1.6, IC1.2 (OUT)
VDC: C1.+, C2.+, C3.+, C4.+, C5.+, C6.+, C10.2, C11.2, C12.2, C13.2, C14.2, C15.2, CON2.9, CON3.+, D1.C, D2.C, Q1.7 (D), Q1.8 (D), Q1.EP-7-8 (D), Q2.7 (D), Q2.8 (D), Q2.EP-7-8 (D), Q3.7 (D), Q3.8 (D), Q3.EP-7-8 (D)
VDD_5V: CON1.1, R9.2

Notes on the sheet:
PHASE_A
PHASE_B
PHASE_C
A bulk capacitor is required (not shown on this schematic). Its exact capacitance depends on the maximum power rating of the device.
Capacitor battery
These capacitors should be placed as close as possible to the power transistors.
Temperature sensor
Battery connection
The minimum specific bulk capacitance is 20 μF/A (e.g. an ESC rated for 20 A DC requires at least 400 μF).
Place ground and power ground junction as close to negative supply pad as possible
Place close to power mosfets
1727-7274-1-ND MOSFET 2N-CH 40V 40A LFPAK56D 1727-2462-1-ND MOSFET 2N-CH 60V 40A LFPAK56
the only difference between 8S and 10S versions is MOSFET and capacitor selection
732-8860-1-ND 68uF 50V capacitor

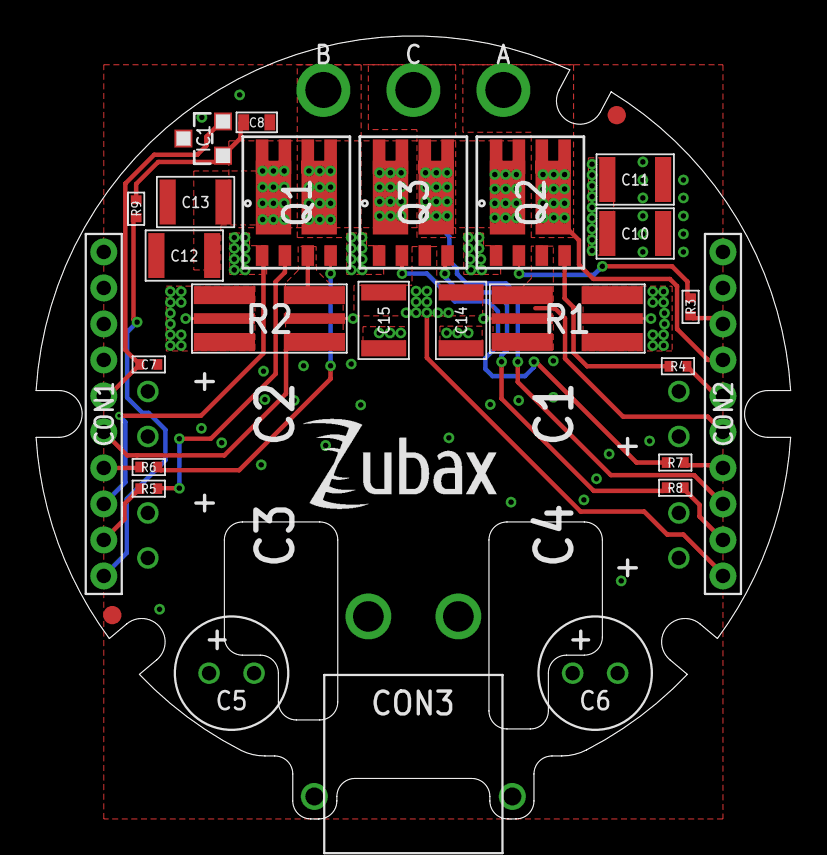
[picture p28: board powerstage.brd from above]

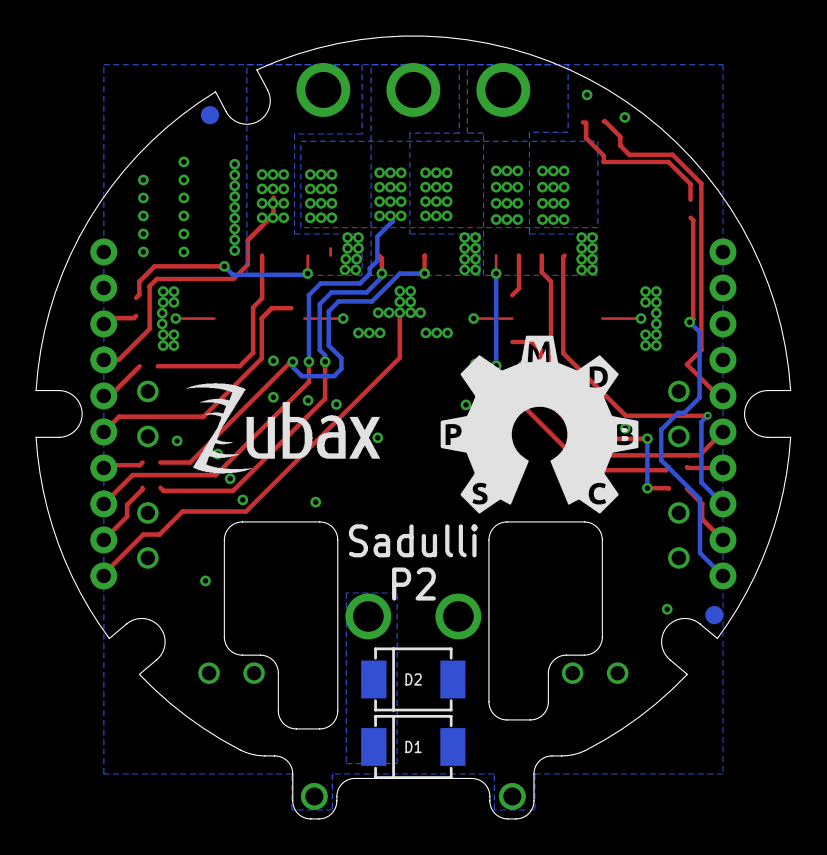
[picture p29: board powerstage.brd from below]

Board: 4 copper layers, 41.9 x 43.5 mm, 44 parts (6 on the bottom side), 27 nets.

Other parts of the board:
U$1, U$13: ZUBAX_LOGO_5X10
U$2: DUCK_6X5
U$4: OSHW-10.5X11.5

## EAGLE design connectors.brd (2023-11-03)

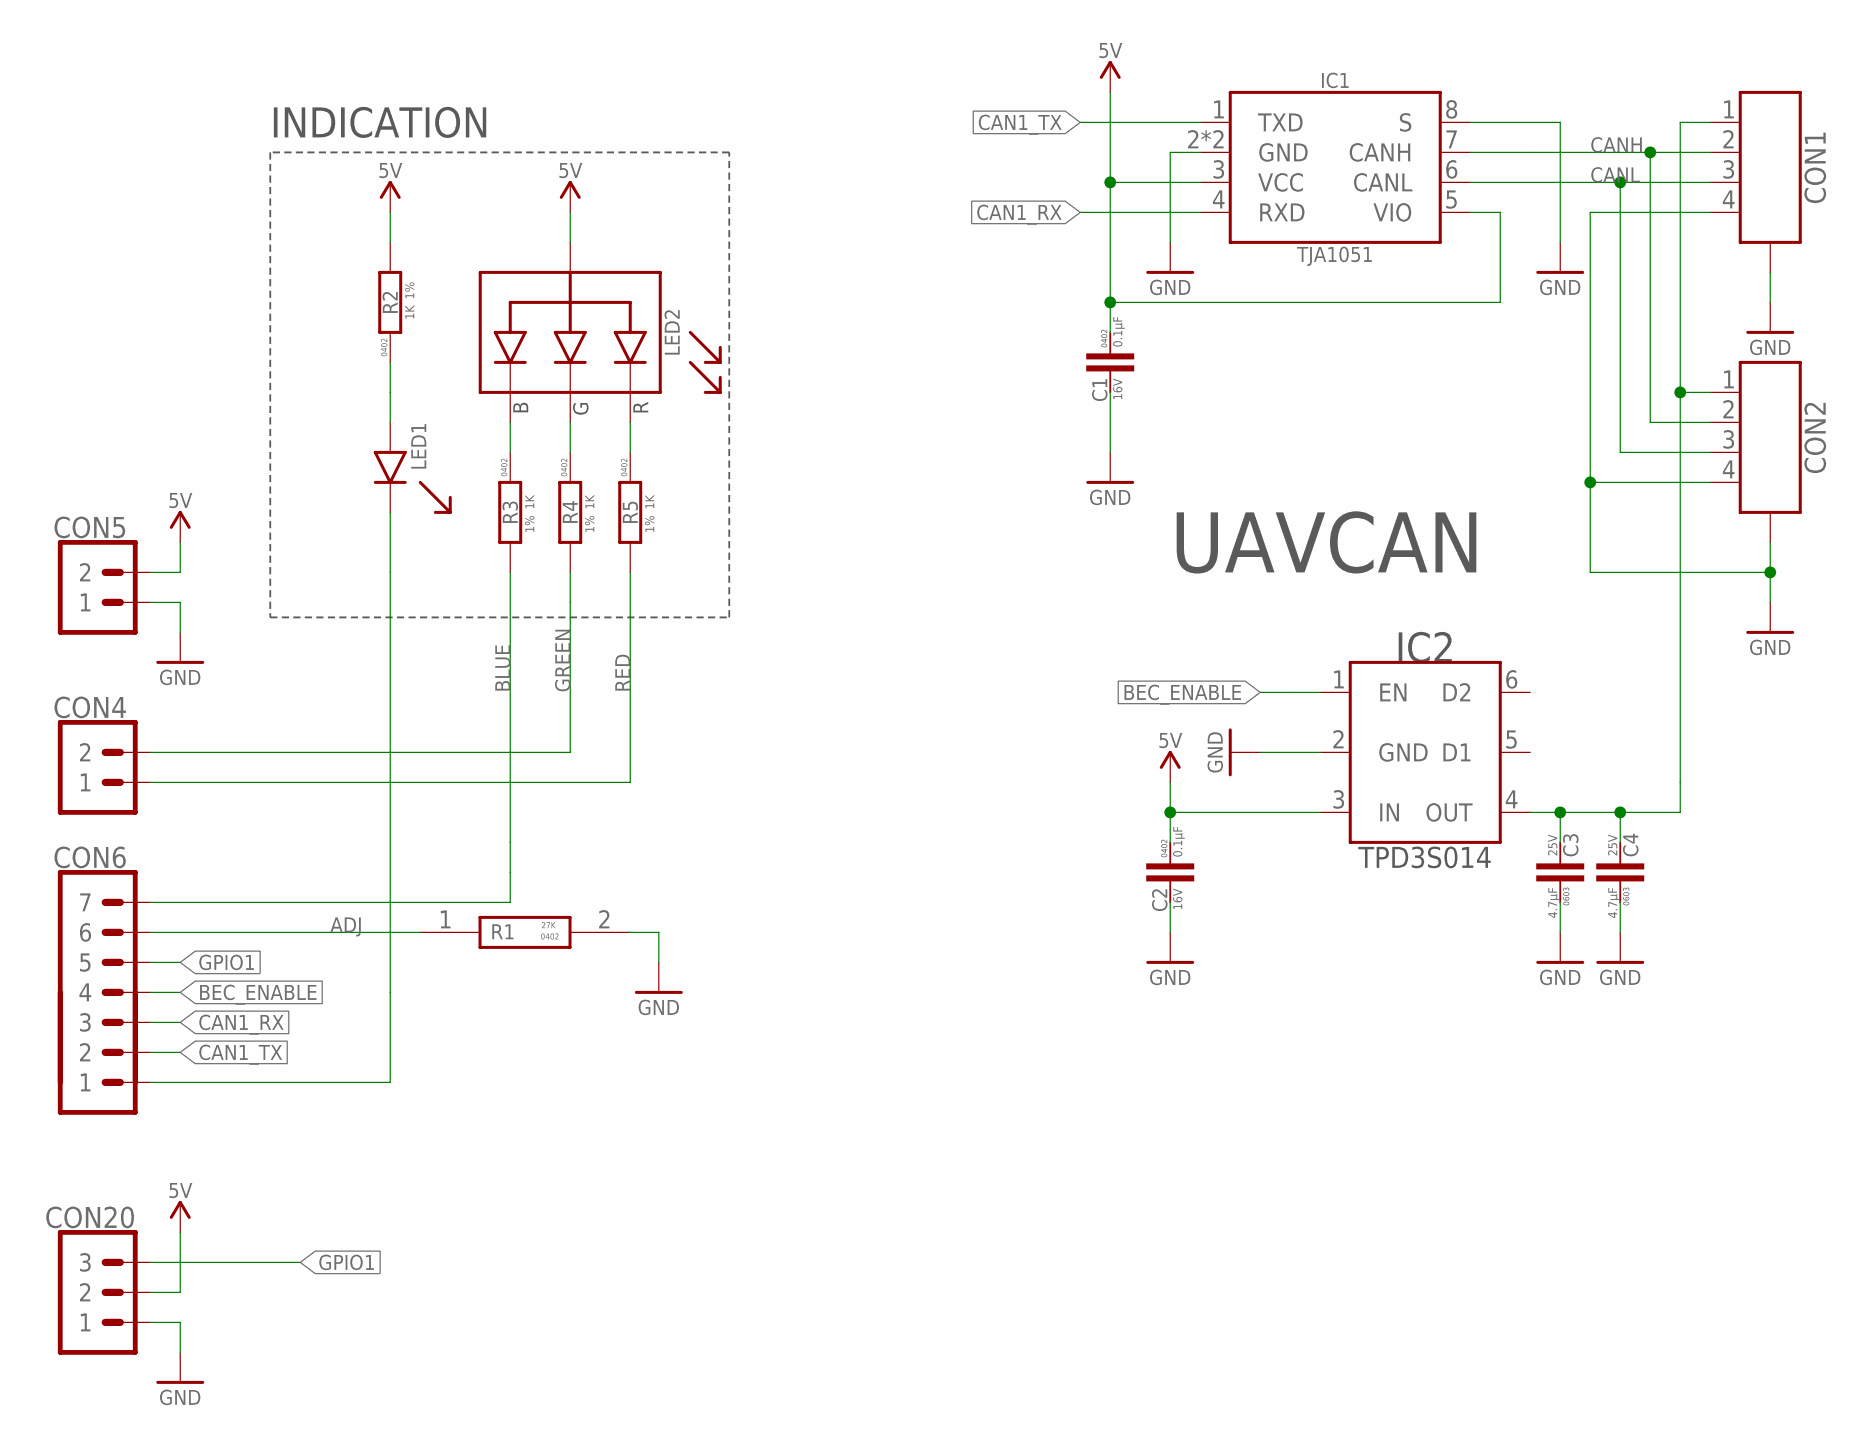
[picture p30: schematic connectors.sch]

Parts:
C1, C2: 0.1µF; C0402
C3, C4: 4.7µF; C0603
CON1, CON2: CON-4P-TABS-JST_GH-RA; JST_GH-4P-RA
CON4, CON5: PINHEAD_1X02-2; 1X02-PTH-2
CON6: PINHEAD_1X07-2; 1X07-PTH-2
CON20: PINHEAD_1X03-2.54-RA; 1X03-PTH-2.54-RA
IC1: TJA1051; SOT782-1
IC2: TPD3S014DBVR-SOT23-6; SOT26
LED1: GREEN; 0402_LED
LED2: LTST-C19HE1WT; LITE_ON_RGB_LED
R1: 27K; RESC1005X40N; MANUFACTURER_PART_NUMBER AF0402FR-0727KL
R2, R3, R4, R5: 1K; R0402

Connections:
ADJ: CON6.6, R1.1
BEC_ENABLE: CON6.4, IC2.1 (EN)
BLUE: CON6.7, R3.2
CAN1_LED: CON6.1, LED1.C
CAN1_RX: CON6.3, IC1.4 (RXD)
CAN1_TX: CON6.2, IC1.1 (TXD)
CAN1_VDD: C3.P$2 (2), C4.P$2 (2), CON1.1, CON2.1, IC2.4 (OUT)
CANH: CON1.2, CON2.2, IC1.7 (CANH)
CANL: CON1.3, CON2.3, IC1.6 (CANL)
GND: C1.2, C2.2, C3.P$1 (1), C4.P$1 (1), CON1.4, CON1.M$0 (GND), CON1.M$1 (GND), CON2.4, CON2.M$0 (GND), CON2.M$1 (GND), CON5.1, CON20.1, IC1.2 (GND), IC1.8 (S), IC1.PAD (GND), IC2.2 (GND), R1.2
GPIO1: CON6.5, CON20.3
GREEN: CON4.2, R4.2
unnamed: LED1.A, R2.1
unnamed: LED2.R, R5.1
unnamed: LED2.G, R4.1
unnamed: LED2.B, R3.1
RED: CON4.1, R5.2
VDD_5V: C1.1, C2.1, CON5.2, CON20.2, IC1.3 (VCC), IC1.5 (VIO), IC2.3 (IN), LED2.+ (A), R2.2

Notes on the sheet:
INDICATION
UAVCAN

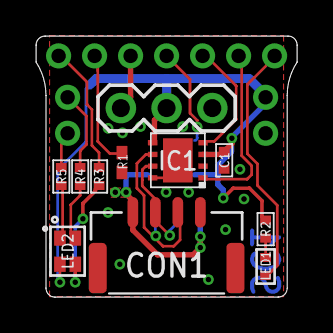
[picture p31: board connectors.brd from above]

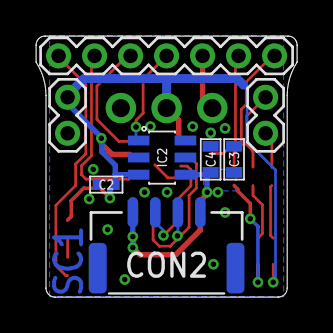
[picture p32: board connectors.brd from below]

Board: 2 copper layers, 14.5 x 14.5 mm, 19 parts (8 on the bottom side), 18 nets.

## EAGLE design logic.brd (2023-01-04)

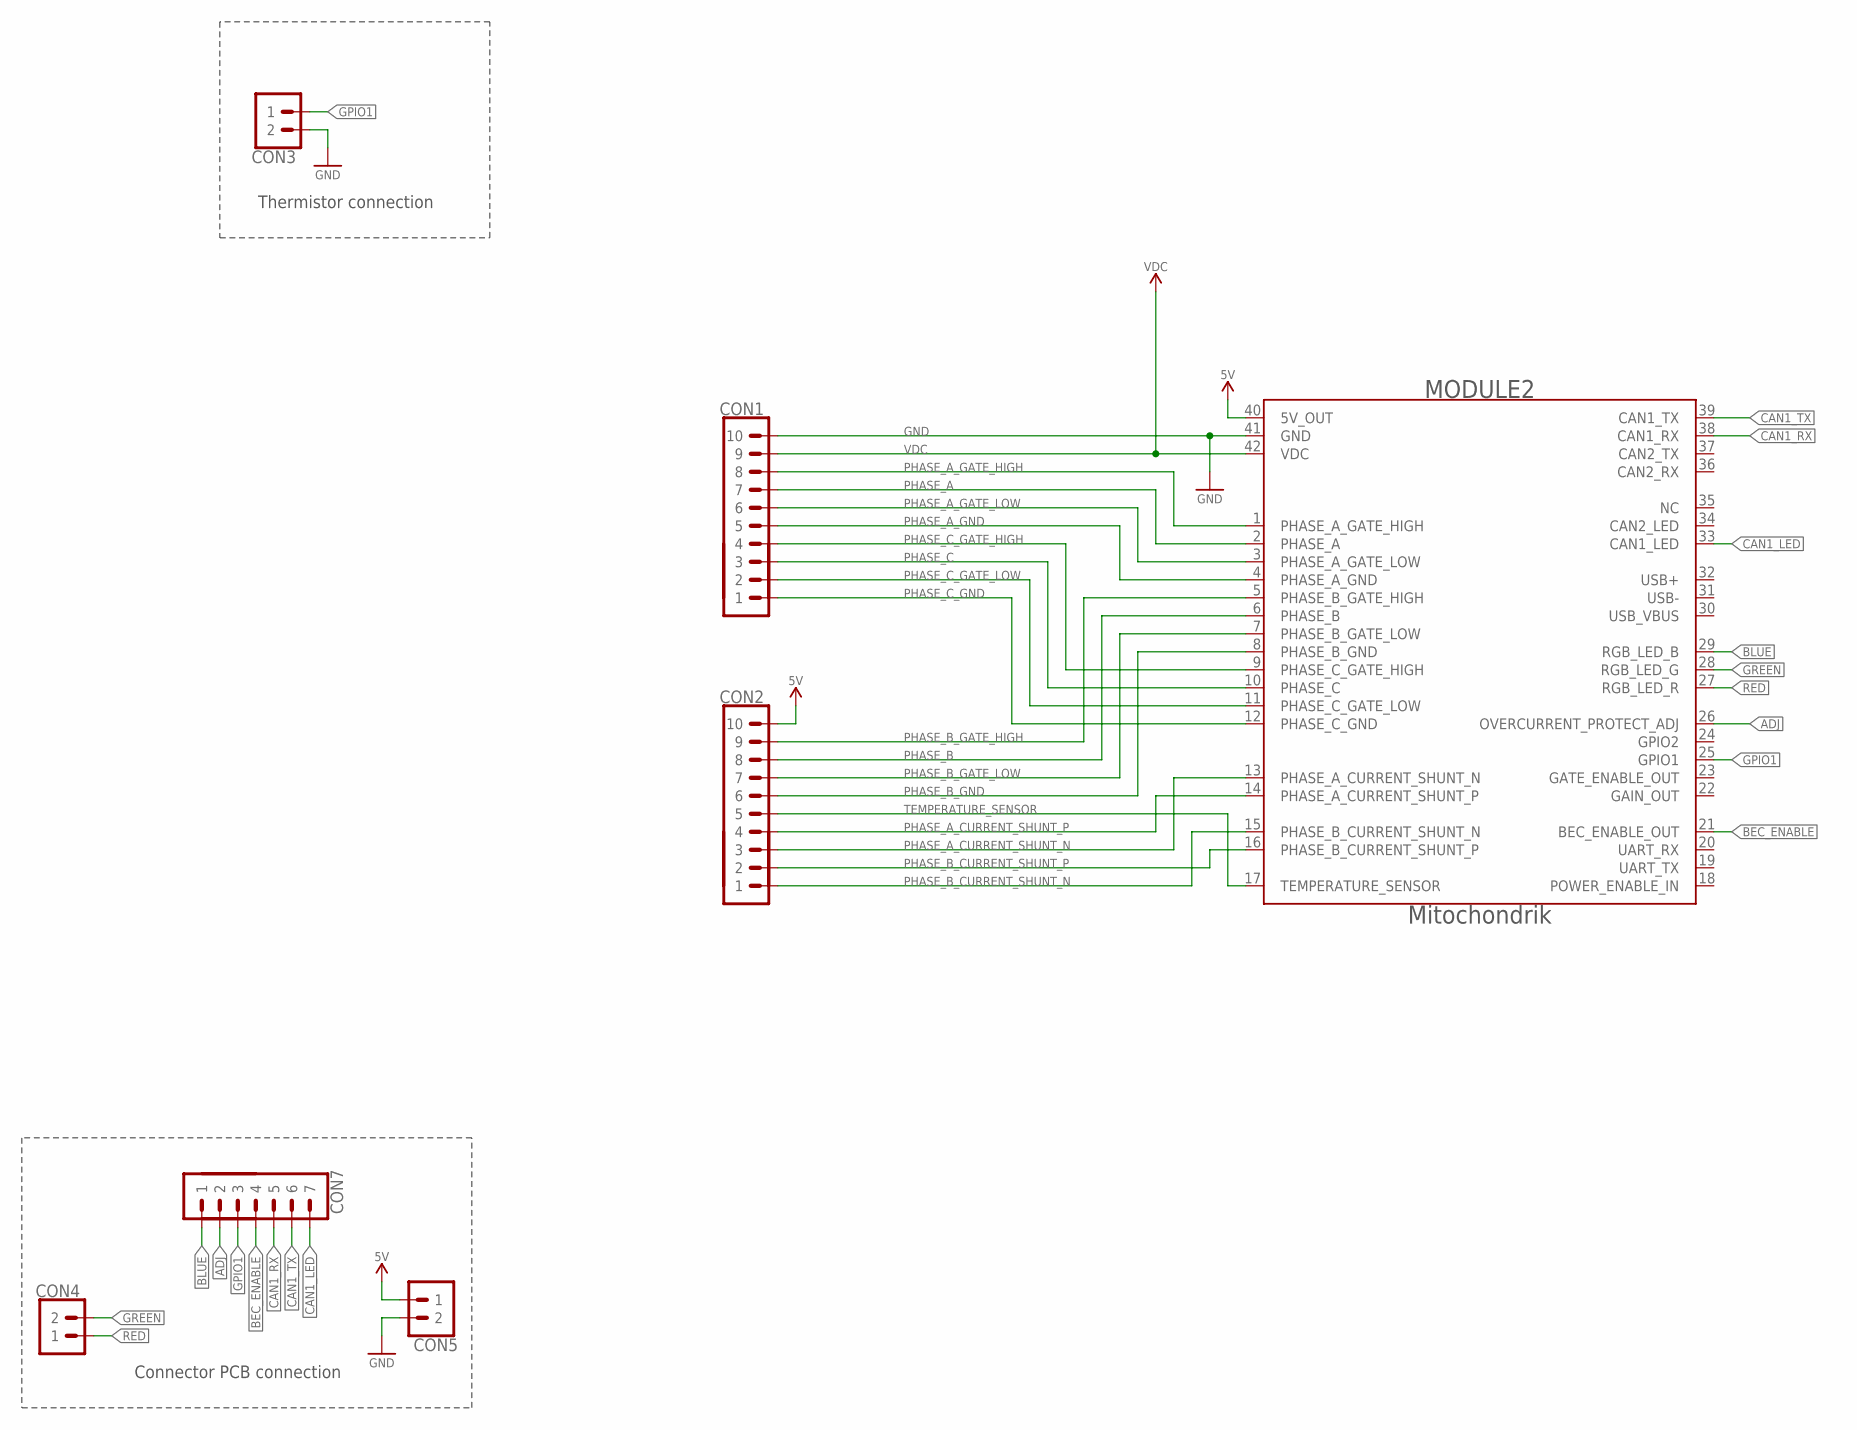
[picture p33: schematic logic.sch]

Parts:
CON1, CON2: PINHEAD_1X10-2; 1X10-PTH_2
CON3, CON4, CON5: PINHEAD_1X02-2; 1X02-PTH-2
CON7: PINHEAD_1X07-2; 1X07-PTH-2
MODULE2: MITOHONDRIQUE_V0.2-TH; MITOHONDRIQUE-TH

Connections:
ADJ: CON7.2, MODULE2.26 (OVERCURRENT_PROTECT_ADJ)
BEC_ENABLE: CON7.4, MODULE2.21 (BEC_ENABLE_OUT)
BLUE: CON7.1, MODULE2.29 (RGB_LED_B)
CAN1_LED: CON7.7, MODULE2.33 (CAN1_LED)
CAN1_RX: CON7.5, MODULE2.38 (CAN1_RX)
CAN1_TX: CON7.6, MODULE2.39 (CAN1_TX)
GND: CON1.10, CON3.2, CON5.2, MODULE2.41 (GND)
GPIO1: CON3.1, CON7.3, MODULE2.25 (GPIO1)
GREEN: CON4.2, MODULE2.28 (RGB_LED_G)
PHASE_A: CON1.7, MODULE2.2 (PHASE_A)
PHASE_A_CURRENT_SHUNT_N: CON2.3, MODULE2.13 (PHASE_A_CURRENT_SHUNT_N)
PHASE_A_CURRENT_SHUNT_P: CON2.4, MODULE2.14 (PHASE_A_CURRENT_SHUNT_P)
PHASE_A_GATE_HIGH: CON1.8, MODULE2.1 (PHASE_A_GATE_HIGH)
PHASE_A_GATE_LOW: CON1.6, MODULE2.3 (PHASE_A_GATE_LOW)
PHASE_A_GND: CON1.5, MODULE2.4 (PHASE_A_GND)
PHASE_B: CON2.8, MODULE2.6 (PHASE_B)
PHASE_B_CURRENT_SHUNT_N: CON2.1, MODULE2.15 (PHASE_B_CURRENT_SHUNT_N)
PHASE_B_CURRENT_SHUNT_P: CON2.2, MODULE2.16 (PHASE_B_CURRENT_SHUNT_P)
PHASE_B_GATE_HIGH: CON2.9, MODULE2.5 (PHASE_B_GATE_HIGH)
PHASE_B_GATE_LOW: CON2.7, MODULE2.7 (PHASE_B_GATE_LOW)
PHASE_B_GND: CON2.6, MODULE2.8 (PHASE_B_GND)
PHASE_C: CON1.3, MODULE2.10 (PHASE_C)
PHASE_C_GATE_HIGH: CON1.4, MODULE2.9 (PHASE_C_GATE_HIGH)
PHASE_C_GATE_LOW: CON1.2, MODULE2.11 (PHASE_C_GATE_LOW)
PHASE_C_GND: CON1.1, MODULE2.12 (PHASE_C_GND)
RED: CON4.1, MODULE2.27 (RGB_LED_R)
TEMPERATURE_SENSOR: CON2.5, MODULE2.17 (TEMPERATURE_SENSOR)
VDC: CON1.9, MODULE2.42 (VDC)
VDD_5V: CON2.10, CON5.1, MODULE2.40 (5V_OUT)

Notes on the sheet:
Thermistor connection
Connector PCB connection

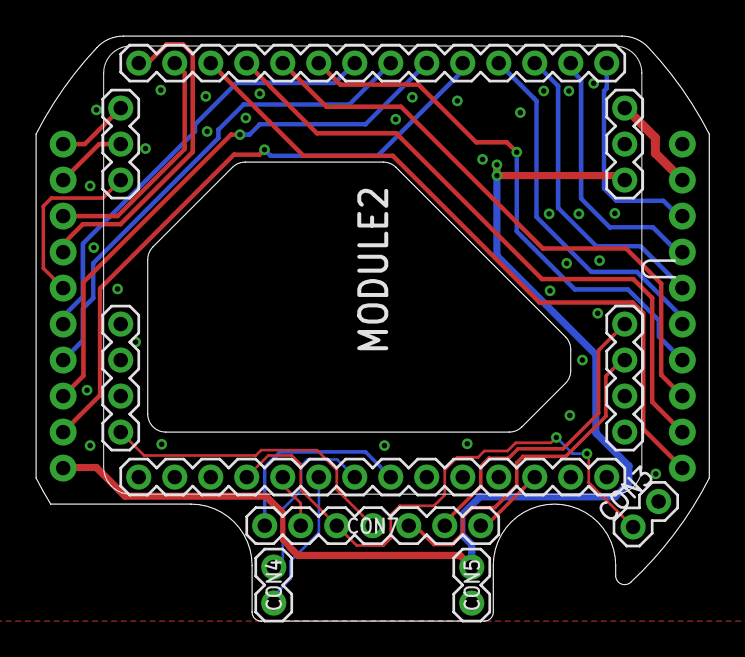
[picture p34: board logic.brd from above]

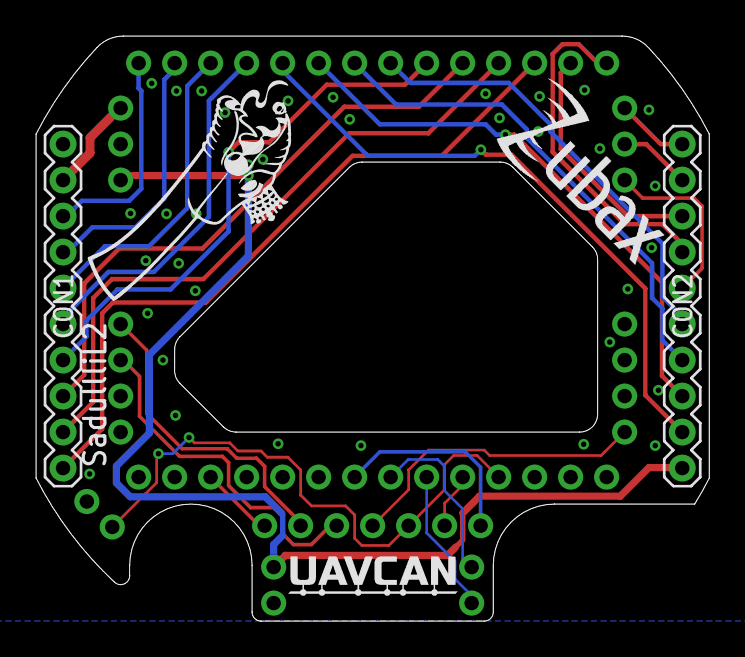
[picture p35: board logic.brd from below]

Board: 2 copper layers, 37.4 x 32.5 mm, 10 parts (5 on the bottom side), 29 nets.

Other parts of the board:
U$1: ZUBAX_LOGO_5X10
U$3: UAVCAN_9X2.5
U$5: DRAGON-15X6

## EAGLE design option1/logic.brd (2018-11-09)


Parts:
CON1, CON2: PINHEAD_1X10-2; 1X10-PTH_2
CON3: PINHEAD_1X06-2; 1X06-PTH-2
CON4, CON5, CON6: PINHEAD_1X02-2; 1X02-PTH-2
MODULE2: MITOHONDRIQUE-TH; MITOHONDRIQUE

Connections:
ADJ: CON3.2, MODULE2.29 (OVERCURRENT_PROTECT_ADJ)
BLUE: CON3.1, MODULE2.32 (RGB_LED_B)
CAN1_LED: CON3.6, MODULE2.36 (CAN1_LED)
CAN1_RX: CON3.4, MODULE2.41 (CAN1_RX)
CAN1_TX: CON3.5, MODULE2.42 (CAN1_TX)
GND: CON1.10, CON5.2, CON6.2, MODULE2.2 (GND)
GPIO1: CON3.3, CON6.1, MODULE2.27 (GPIO1)
GPIO2: MODULE2.28 (GPIO2)
GREEN: CON4.2, MODULE2.31 (RGB_LED_G)
unnamed: CON2.3, MODULE2.18 (PHASE_B_CURRENT_SHUNT_N)
unnamed: CON2.2, MODULE2.17 (PHASE_A_CURRENT_SHUNT_P)
unnamed: CON2.1, MODULE2.16 (PHASE_A_CURRENT_SHUNT_N)
unnamed: CON2.4, MODULE2.19 (PHASE_B_CURRENT_SHUNT_P)
unnamed: CON1.1, MODULE2.15 (PHASE_C_GND)
PHASE_A: CON1.7, MODULE2.5 (PHASE_A)
PHASE_A_GATE_HIGH: CON1.8, MODULE2.4 (PHASE_A_GATE_HIGH)
PHASE_A_GATE_LOW: CON1.6, MODULE2.6 (PHASE_A_GATE_LOW)
PHASE_A_GND: CON1.5, MODULE2.7 (PHASE_A_GND)
PHASE_B: CON1.3, MODULE2.13 (PHASE_C)
PHASE_B_GATE_HIGH: CON1.4, MODULE2.12 (PHASE_C_GATE_HIGH)
PHASE_B_GATE_LOW: CON1.2, MODULE2.14 (PHASE_C_GATE_LOW)
PHASE_C: CON2.8, MODULE2.9 (PHASE_B)
PHASE_C_GATE_HIGH: CON2.9, MODULE2.8 (PHASE_B_GATE_HIGH)
PHASE_C_GATE_LOW: CON2.7, MODULE2.10 (PHASE_B_GATE_LOW)
PHASE_C_GND: CON2.6, MODULE2.11 (PHASE_B_GND)
RED: CON4.1, MODULE2.30 (RGB_LED_R)
TEMPERATURE_SENSOR: CON2.5, MODULE2.20 (TEMPERATURE_SENSOR)
VDC: CON1.9, MODULE2.3 (VDC)
VDD_5V: CON2.10, CON5.1, MODULE2.1 (5V_OUT)

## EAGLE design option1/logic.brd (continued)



Board: 2 copper layers, 37.4 x 32.5 mm, 8 parts (3 on the bottom side), 28 nets.

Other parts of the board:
U$1: ZUBAX_LOGO_5X10

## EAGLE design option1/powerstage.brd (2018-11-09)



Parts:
A: PAD-HOLE_2; HOLE_2
B: PAD-HOLE_2; HOLE_2
C: PAD-HOLE_2; HOLE_2
C1, C2, C3, C4: CPOLRADIAL-6.3X12.5-RA; RADIAL_6.3X12.5-RA
C5, C6: CPOL-RADIAL_6.3X12.5; RADIAL_6.3X12.5
C13: 0.1µF; C0402
C14: 4.7µF; C0603
C31, C35, C58, C62, C63, C64: 4.7µF; C1210
CON1, CON3: PINHEAD_1X10-2-FEMALE; 1X10-PTH_2-FEMALE
CON2: BATTERY_CON-2P-XT30-RA; XT30-RA
D1, D2, D3, D4: PTVS36VP1UP,115-36V-SOD128; SOD128
IC5: MCP9700; SOT23B-3
Q1, Q2, Q3: BUK7K6R2-40EX; SOT-1205
R2, R3, R15, R16, R22, R23: 4R3; R0402
R5, R18: 1 mOhms; R2512-KELVIN
R27: 200R; R0402
S1: SENSE; SENSE-0.6

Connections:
GND: CON3.10
unnamed: Q2.2 (G), R2.2
unnamed: Q2.4 (G), R3.2
unnamed: Q1.2 (G), R15.2
unnamed: Q1.4 (G), R16.2
unnamed: C14.P$2 (2), IC5.1 (VCC), R27.1
unnamed: Q3.2 (G), R22.2
unnamed: Q3.4 (G), R23.2
PGND: C1.-, C2.-, C3.-, C4.-, C5.-, C6.-, C13.1, C14.P$1 (1), C31.1, C35.1, C58.1, C62.1, C63.1, C64.1, CON2.-, D1.A, D2.A, D3.A, D4.A, IC5.3 (GND), Q3.3 (S), R5.2, R5.22 (2), R18.2, R18.22 (2), S1.SHELL (SHELLL)
PHASE_A: A.P$1, CON3.7, Q2.1 (S), Q2.5 (D), Q2.6 (D), Q2.EP-5-6 (D)
PHASE_A_CURRENT_SHUNT_N: CON1.8, R5.S1
PHASE_A_CURRENT_SHUNT_P: CON1.7, R5.S2
PHASE_A_GATE_HIGH: CON3.8, R2.1
PHASE_A_GATE_LOW: CON3.6, R3.1
PHASE_A_GND: CON3.5, Q2.3 (S), R5.1, R5.11 (1)
PHASE_B: B.P$1, CON1.3, Q1.1 (S), Q1.5 (D), Q1.6 (D), Q1.EP-5-6 (D)
PHASE_B_CURRENT_SHUNT_N: CON1.10, R18.S1
PHASE_B_CURRENT_SHUNT_P: CON1.9, R18.S2
PHASE_B_GATE_HIGH: CON1.2, R15.1
PHASE_B_GATE_LOW: CON1.4, R16.1
PHASE_B_GND: CON1.5, Q1.3 (S), R18.1, R18.11 (1)
PHASE_C: C.P$1, CON3.3, Q3.1 (S), Q3.5 (D), Q3.6 (D), Q3.EP-5-6 (D)
PHASE_C_GATE_HIGH: CON3.4, R22.1
PHASE_C_GATE_LOW: CON3.2, R23.1
PHASE_C_GND: CON3.1, S1.IN
TEMPERATURE_SENSOR: C13.2, CON1.6, IC5.2 (OUT)
VDC: C1.+, C2.+, C3.+, C4.+, C5.+, C6.+, C31.2, C35.2, C58.2, C62.2, C63.2, C64.2, CON2.+, CON3.9, D1.C, D2.C, D3.C, D4.C, Q1.7 (D), Q1.8 (D), Q1.EP-7-8 (D), Q2.7 (D), Q2.8 (D), Q2.EP-7-8 (D), Q3.7 (D), Q3.8 (D), Q3.EP-7-8 (D)
VDD_5V: CON1.1, R27.2

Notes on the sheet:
PHASE_A
PHASE_B
PHASE_C
A bulk capacitor is required (not shown on this schematic). Its exact capacitance depends on the maximum power rating of the device.
Capacitor battery
These capacitors should be placed as close as possible to the power transistors.
Temperature sensor
Battery connection
The minimum specific bulk capacitance is 20 μF/A (e.g. an ESC rated for 20 A DC requires at least 400 μF).
Place ground and power ground junction as close to negative supply pad as possible
Place close to power mosfets



Board: 4 copper layers, 42.0 x 43.5 mm, 40 parts (3 on the bottom side), 27 nets.

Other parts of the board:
U$1, U$13: ZUBAX_LOGO_5X10

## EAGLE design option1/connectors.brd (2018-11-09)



Board: 2 copper layers, 13.0 x 14.5 mm, 15 parts (4 on the bottom side), 17 nets.

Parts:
C11: 0.1µF; C0402
CON1: PINHEAD_1X06-2; 1X06-PTH-2
CON2: PINHEAD_1X03-2.54-RA; 1X03-PTH-2.54-RA
CON3, CON8: CON-4P-JST_GH-RA; JST_GH-4P-RA
CON4, CON5: PINHEAD_1X02-2; 1X02-PTH-2
IC3: TJA1051; SOT782-1
LED1: GREEN; 0402_LED
LED2: LTST-C19HE1WT; LITE_ON_RGB_LED
R1, R10, R11, R12, R13: 1K; R0402

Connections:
ADJ: CON1.5, R1.2
BLUE: CON1.6, R11.2
CAN1_LED: CON1.1, LED1.C
CAN1_RX: CON1.3, IC3.4
CAN1_TX: CON1.2, IC3.1
GND: C11.2, CON2.1, CON3.4, CON3.M$0, CON3.M$1, CON5.1, CON8.4, CON8.M$0, CON8.M$1, IC3.2, IC3.8, IC3.PAD, R1.1
GPIO1: CON1.4, CON2.3
GREEN: CON4.2, R12.2
unnamed: LED1.A, R10.1
unnamed: CON3.2, CON8.2, IC3.7
unnamed: CON3.1, CON8.1
unnamed: CON3.3, CON8.3, IC3.6
unnamed: LED2.R, R13.1
unnamed: LED2.G, R12.1
unnamed: LED2.B, R11.1
RED: CON4.1, R13.2
VDD_5V: C11.1, CON2.2, CON5.2, IC3.3, IC3.5, LED2.+, R10.2

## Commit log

2018-11-08 initial import
    [logic.brd, logic.sch, powerstage.brd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]
2018-11-08 silk updates
    [logic.brd, logic.sch, powerstage.brd]
2018-11-09 updates here and there
    [connectors.brd, logic.brd, logic.sch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]
2018-11-09 Roting is completed
    [connectors.brd, connectors.sch, logic.brd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]
2018-11-09 routing finished
    [connectors.brd, connectors.sch, logic.brd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]
2018-11-09 pcb outline updated
    [logic.brd]
2018-11-09 powerstage polygones fixes
    [powerstage.brd]
2018-11-09 logic board outline fix
    [logic.brd]
2018-11-09 powerstage updates
    [powerstage.brd, powerstage.sch]
2018-11-09 BOM added
    [BOM.csv]
2018-11-09 DUCK is here
    [powerstage.brd, powerstage.sch]
2018-11-10 OSHW logo
    [powerstage.brd]
2018-11-10 here comes UAVCAN BEC output
    [connectors.brd, connectors.sch]
2018-11-11 Routing is complete again. Now with BEC output
    [connectors.brd, connectors.sch, logic.brd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]
2018-11-11 proper powerstage outline
    [powerstage.brd]
2018-11-11 bloody connectors had to be moved
    [powerstage.brd]
2018-11-11 bloody connectors
    [logic.brd]
2018-11-11 minor mask fixes
    [connectors.brd, logic.brd, powerstage.brd]
2018-11-11 inner layers update
    [powerstage.brd]
2018-11-11 connectors pcb outline update
    [connectors.brd]
2018-11-11 connectors pcb fillets
    [connectors.brd]
2018-11-11 poly update
    [powerstage.brd, powerstage.sch]
2018-11-12 pinout fixes
    [connectors.brd, logic.brd, logic.sch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]
2018-11-12 gerber files added
2018-11-12 powerstage 40V version BOM
    [BOM.csv]
2018-11-12 fiducial marks
    [connectors.brd, connectors.sch, powerstage.brd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]
2018-11-12 powerstage assembly files
    [powerstage.brd, powerstage.sch]
2018-11-12 connectors PCB BOM
    [bom.csv]
2018-11-12 more assembly drawings added
2018-11-12 logic PCB BOM
    [BOM.csv]
2018-11-26 Logic board update.
    Thermistor connection moved to other side of the PCB
    [logic.brd, logic.sch]
2018-11-26 1210 ceramic capacitors replaced with better ones
    [powerstage.brd, powerstage.sch]
2018-11-27 fixed logic board to fit housing better
    [logic.brd, logic.sch]
2018-12-17 updated compnents naming. Updated production docs
    [bom.csv, connectors.brd, connectors.sch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]
2019-03-27 PCB stack files added
2019-03-27 PCB stack updates
    [connectors.brd, powerstage.brd]
2019-03-27 UAVCAN logo
    [logic.brd]
2019-03-28 link to the BOM spreadsheet
2019-03-29 let there be a giant hole in the middle of the PCB
    [logic.brd, logic.sch]
2019-03-29 Library update
    [connectors.brd, connectors.sch]
2019-03-29 let there be holes in powerstage as well
    [powerstage.brd, powerstage.sch]
2019-03-29 Silkscreen fix
    [powerstage.brd]
2019-03-29 Bloody fiducial marks
    [powerstage.brd]
2019-03-29 damn duck logo
    [powerstage.brd, powerstage.sch]
2019-03-30 offline BOM added
    [BOM.xlsx]
2019-04-06 TVS diode replaced
    [powerstage.brd, powerstage.sch]
2020-01-06 migration to the latest version of mitochondrik library
    [logic.brd, logic.sch]
2021-01-05 Assembly instructions (#8)
2023-01-04 Key added (#14)
    [logic.brd]
2023-05-08 Alakdan & assembly (#16)
    * updated assembly
    closes #15
    - updated assembly guide
    - replaced motor
    - replaced thermistor specification
    - updated Sadulli version
    - updated Sadulli readme
    - added Alakdan photos
    need to update main README table for Alakdan
    * updated table
    * Update README.md
    * Update assembly_instructions/readme.md
    * requested changes
    - replaced UAVCAN with Cyphal & added link to telega.zubax.com
    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
    [connectors.brd, connectors.sch]
2023-05-15 updated attributes (#19)
    added MANF and MANF# attributes to the connectors and powerstage schematics
    [connectors.brd, connectors.sch, powerstage.brd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]
2023-11-03 set reference points for assembling MOSFETs and LED (#21)
    [connectors.brd, powerstage.brd]
2024-04-24 Update README.md (#23)
    added maximum continuous phase current amplitude 40 A
